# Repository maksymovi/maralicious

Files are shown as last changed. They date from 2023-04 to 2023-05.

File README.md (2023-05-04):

# Maralicious: A MaraX Display Mod

This is a work in progress display for the Lelit MaraX, primarily an automatic shot timer for the LilyGo T-Display. Still very much a work in progress but basic functionality is there.

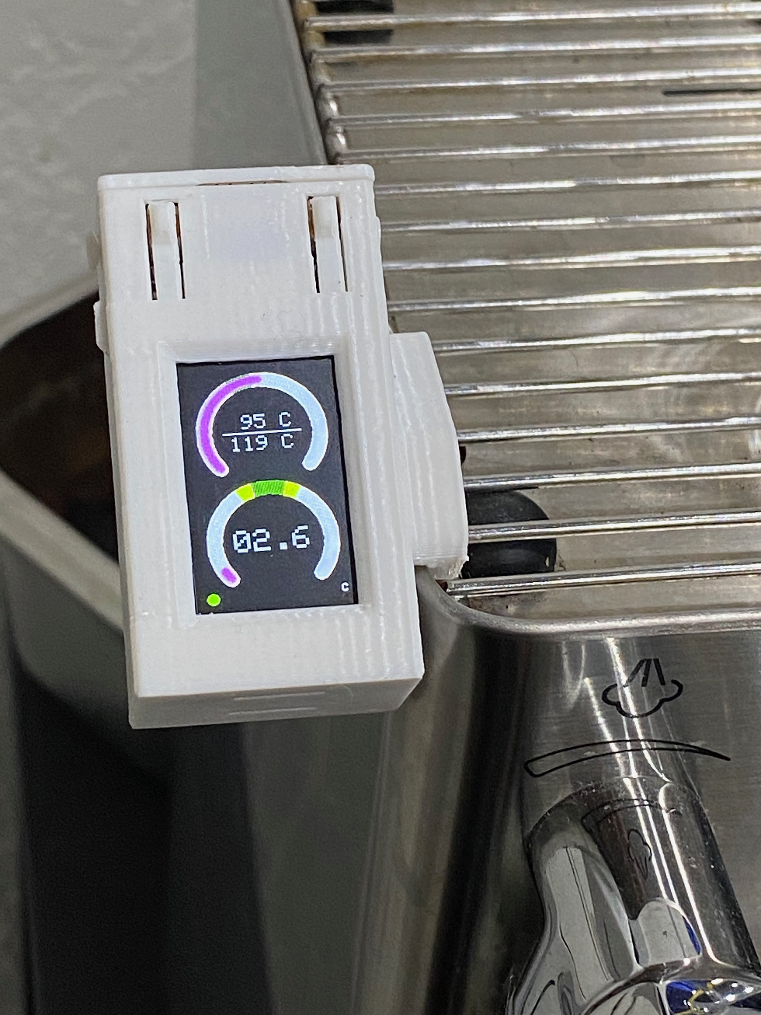
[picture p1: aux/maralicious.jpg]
Image of maralicious running on a T-Display


## Current and to be done functionality:

- [x] Shot timer
- [x] Read serial port and display useful data (temperature, heater on or off, steam or brew mode)
- [x] Connect to wifi and dump serial output to wifi
- [ ] Polish display (purple dials probably isn't the best ux)
- [ ] Stretch goal: Serve webpage with relevant graphs about (if memory constraints allow)

## The journey and the hardware

I more or less started working on this immediately after getting my Mara. Maybe it would've been easier to buy a machine that already displays this data but this machine was too good a deal to not get and I like tinkering with things anyways.

It runs on a LilyGo T-Display for now, may upgrade to the T-Display S3 in the future, but this should work for basically any LilyGo product. A number of other Mara monitors on Github run the T-Display and this originally started with me just wanting to get one of those running before being dissatisfied and deciding to make my own. It's cheap, 10 bucks a pop, I liked them enough I bought a few extras for other shenanigans. Initially this was somewhat inspired by [benovic/mara_display](https://github.com/benovic/marax_display) but all of the code is written by me. 

The serial port is connected through some wires to the T-Display, [see here how to connect them](https://www.reddit.com/r/espresso/comments/hft5zv/data_visualisation_lelit_marax_mod/). Getting this working was somewhat trivial.

The bigger thing was figuring out how to mount the thing onto the Mara, I settled on figuring out how to get it just to clip onto the top of the Mara since it seemed very clippable, and thankfully I have a 3D printer and 9th grade CAD modeling skill. Since creating a case from scratch seemed like a pain I settled on taking an existing case and modifying it in Fusion to clip and have an inlet for wires, resulting in the files inside ```cad```. This was surprisingly successful, although modifying an STL was a bit of a pain, and getting wires to feed into the case is also not easy, but it works and looks pretty. It took a few iterations to get it to clip as close as possible to the front, where there's a hole in the machine for the wires to enter into.

With the case done, I needed to get the pump switch figured out. The timer checks when the pump is running, this took a while to figure out and a few different approaches were tried. First I tried placing a reed switch on the pump, reed switches trigger when in presence of a magnetic field and the pump generates one when on, however connection was very intermittent and didn't work well and the reed switches were super fragile. Figuring out how to place the switch on the pump was also a big pain. 

Second I tried wiring up to the mara switch itself, the switch which actually triggers the pump is a 2 way switch, running 5 volts from the controller back to the controller when the pump needs to run. I tried using an octocoupler to detect when it runs, however this failed as apparently the current flowing through for this signal wire is in the microamps, less than the 1 milliamp needed to trigger the octocoupler. I also tried wiring up to the switch directly, there was a 3rd unused pin on the switch inside connecting the common to it when the switch was off, I was able to get this to work but I was very worried about cross circuit interference/contamination, I had to tie the arduino's ground to the Mara's ground and even then dumping to ground isn't the best idea. I ordered new reed switches thinking those old ones were a fluke and tried again.

The new reed switches also didn't work, but it didn't take me too much debugging to figure out how to solve the problem: **if its an intermittent signal, smooth it out with a capacitor.** I tied a small microfarad capacitor across the reed switch and it was able to fix the signal, it didn't even need any debouncing surprisingly. 

The last thing I needed was power. I ran a risky experiment, the serial port on the mara does supply 5 volts, however it doesn't provide enough current to be able to run the arduino. So instead I just rigged up a 5 volt power brick on the inside, I took an old phone charger, manually soldered the mains to the mains on the mara power button (after figuring out which was the source and which the output), and just hooked up a power brick on the inside. I tried to keep it away from most of the hot parts, and taped what I could to waterproof it a bit. But it got me working power, I was able to solder a custom USB cable of the right length ending in the battery connector for the T-Display.

A bit of code later, I had a working product!

In summary

### Hardware used

* Lelit Mara X 
  * The current code should mostly work for the Mara X V2, however the V2 dumps whether the pump is on or not to the serial port, meaning you do not need the reed switch at all. The code currently does not support this but can be relatively easily modified to do so. 
* LilyGo T-Display
* Reed switch
* Wires with dupont connectors
* 1 microfarad capacitor

## How to run

Assuming you have the arduino ide setup or the VSCode extension for arduino setup, and have the esp32 board module also installed for either of these.

Necessary dependencies are

* Button2 (currently not really used but its included in the code for now until I use it or delete it)
* TFT_eSPI
* WiFi

All should either come with the esp32 board module or can be downloaded from the arduino library manager.

#### IMPORTANT: Setup TFT_eSPI

Within the library folder there should be a file titled "User_Setup_Select.h." You must uncomment the T-Display line (currently Setup25) and **COMMENT #include <User_Setup.h> **. I wasted hours wondering why a quarter of my display was static because I forgot to comment this out. 

If you have some other board supported by TFT_eSPI, the code I've written may work if you enable it but no guarantees, you run everything here at your own risk. 

Beside that, configure the necessary parameters in ```src/config```. The files aren't too hard to read so just give them a scroll through. Compile, upload to your board, and enjoy.

**DO NOT RUN IF YOU DO NOT KNOW WHAT YOU ARE DOING, I TAKE NO RESPONSIBILITY FOR ANY DAMAGE TO YOUR MARA OR ANYTHING ELSE, USE AT YOUR OWN RISK**

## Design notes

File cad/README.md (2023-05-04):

Original design by [Steven Schlueter](https://www.thingiverse.com/stevesch): https://www.thingiverse.com/thing:4813428

I modified the primary case to clip onto the MaraX and have holes for wires to enter.

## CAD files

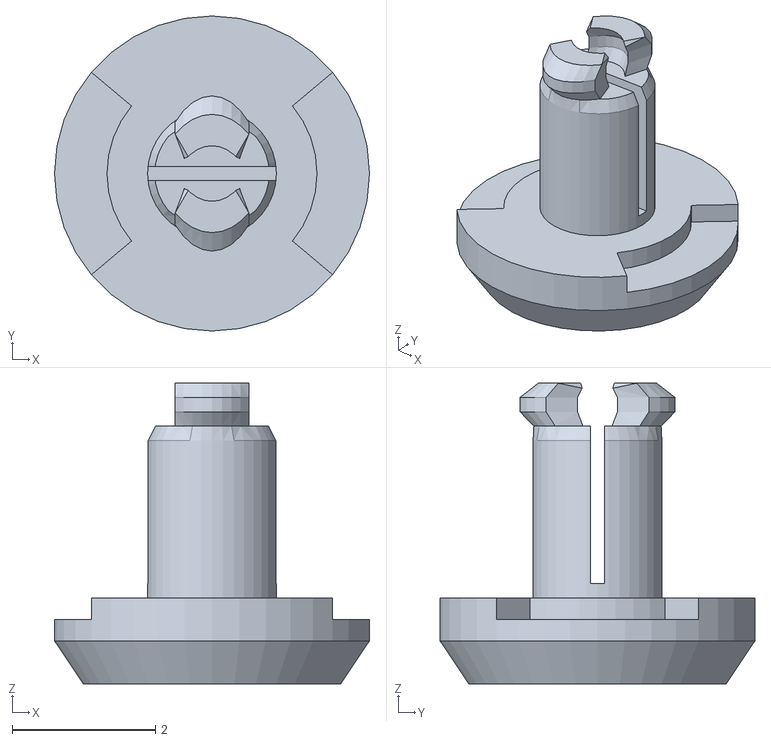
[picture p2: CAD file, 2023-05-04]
cad/esp32-ttgo-headers-lipo401730-v2-pin.STL
4.40 x 4.40 x 4.20

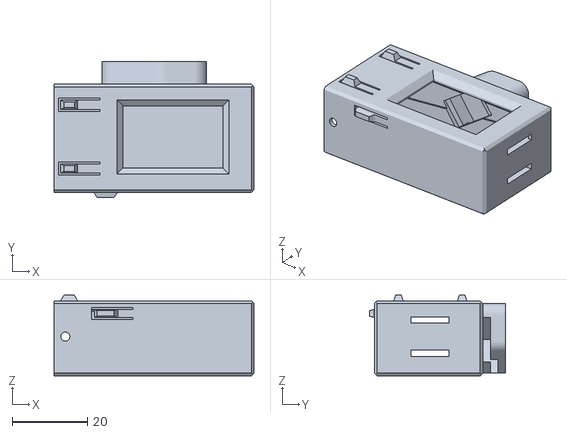
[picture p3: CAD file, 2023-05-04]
cad/esp32-ttgo-headers-lipo401730-v2-body_for_marax.stl
53.0 x 36.1 x 21.4

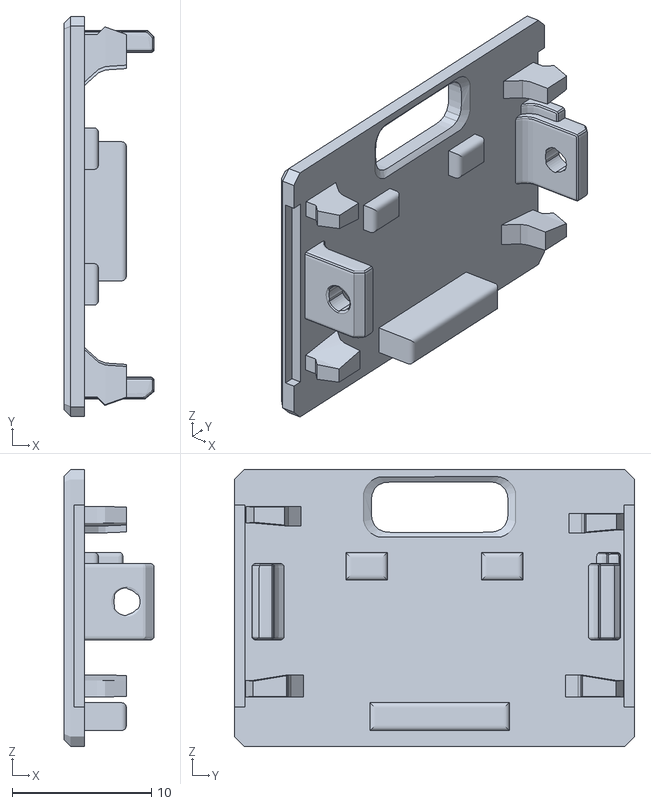
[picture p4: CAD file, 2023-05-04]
cad/esp32-ttgo-headers-lipo401730-v2-cap.STL
6.50 x 28.8 x 19.9

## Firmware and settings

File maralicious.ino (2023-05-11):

#include <Arduino.h>


#include "src/config/secrets.h"
#include "src/config/debug.h"
#include "src/config/pins.h"

#include "src/MaraDisplayer.h"
#include "src/MaraWifiServer.h"
#include "src/MaraSerialReader.h"
#include "src/MaraTimer.h"

MaraDisplayer* md;
MaraWifiServer* mws;
MaraSerialReader* msr;
MaraTimer* mt;

void setup()
{
    Serial.begin(115200);
    Serial.println("Starting setup");

    // timer
    mt = new MaraTimer(PUMP_PIN);
    // display 
    md = new MaraDisplayer();
    // wifi
    mws = new MaraWifiServer(80, wifiSsid, wifiPassword);
    //serial
    msr = MaraSerialReader::getInstance();
    Serial.println("Ending setup");
}

void loop()
{
    char buffer[128];
    MaraSerialReader::MaraXOutput maraXOutput;
    long timer;

    if(msr->readMaraSerial(maraXOutput))
    {
        md->drawTempArc(maraXOutput.hxTemp, maraXOutput.steamTemp);
        md->drawHeaterOnDot(maraXOutput.heaterOn);
        md->drawStatusChar(maraXOutput.steamOrBrew);
        sprintf(buffer, "Read: %s\n", maraXOutput.completeString.c_str());
        mws->broadcastMessage(buffer);
    }
    else
    {
        sprintf(buffer, "Failed to parse :%s\n", maraXOutput.completeString.c_str());
        mws->broadcastMessage(buffer);
    }
    timer = mt->stopwatch();

    md->drawTimerArc(timer);
    delay(100);
}

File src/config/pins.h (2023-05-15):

#pragma once

//DEFINE ONE AND ONLY ONE

//#define T_DISPLAY
#define T_DISPLAY_S3

#ifdef T_DISPLAY

#define PUMP_PIN 27

//black yellow
#define MARAX_TX_PIN 26
//white orange
#define MARAX_RX_PIN 25

#define BUTTONA_PIN  0
#define BUTTONB_PIN  35


#elif defined(T_DISPLAY_S3)

#define PUMP_PIN 16

//black yellow
#define MARAX_TX_PIN 12
//white orange
#define MARAX_RX_PIN 13

#define BUTTONA_PIN  0
#define BUTTONB_PIN  35

#endif

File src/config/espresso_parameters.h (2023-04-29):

#pragma once


//file for various espresso paramteters
#define TARGET_SHOT_TIME 34
#define TARGET_SHOT_TIME_RANGE 4
#define TARGET_SHOT_TIME_LESSER_RANGE 8

#define HX_TARGET_TEMPERATURE 93
#define HX_TARGET_TEMPERATURE_RANGE 4
#define HX_TEMP_LOWER_LIMIT 80
#define HX_TEMP_UPPER_LIMIT 110

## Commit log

2023-04-19 Got basic serial + reed switch pump communcation working with the mara-x
2023-04-29 Got a preliminary timer working, along with a temperature dial
2023-05-04 Got the wifi and serial parsing modules working, something in the code however currently hangs
2023-05-04 Added licenses, readme, generally reorganized the repository
    [esp32-ttgo-headers-lipo401730-v2-body_for_marax.stl, esp32-ttgo-headers-lipo401730-v2-cap.STL, esp32-ttgo-headers-lipo401730-v2-pin.STL]
2023-05-11 Moved timer functions into its own class, minor other debug changes in display
